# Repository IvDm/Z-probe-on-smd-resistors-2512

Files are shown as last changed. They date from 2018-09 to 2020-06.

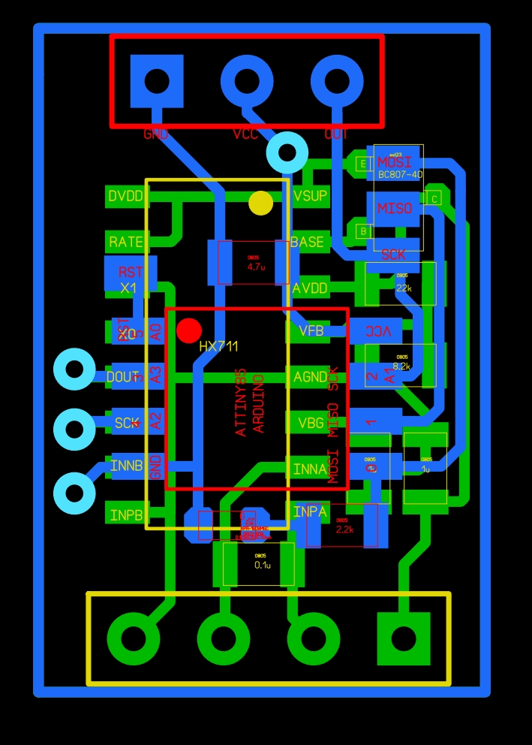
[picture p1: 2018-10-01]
Controller_PCB_TOP.JPG

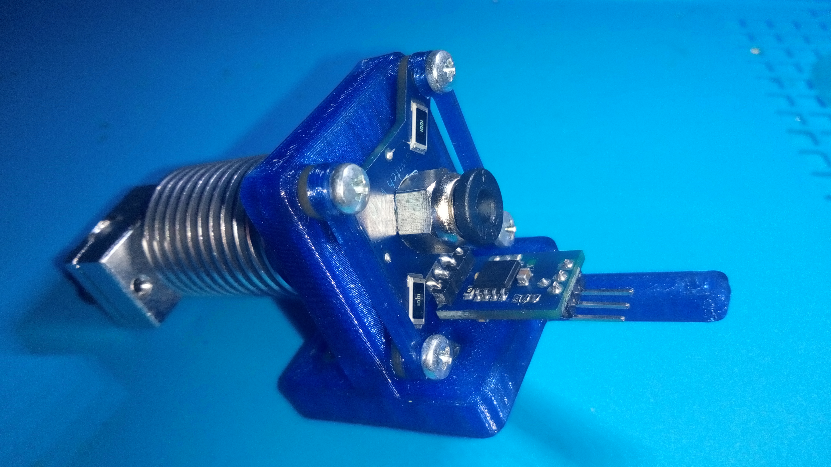
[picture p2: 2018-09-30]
20180930_181452-0.jpg

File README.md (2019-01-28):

# Z-probe-on-smd-resistors-2512
 This project is based on a change in the resistance of resistors under the influence of external factors in particular deformation. The object of the project is to check whether it is possible to use ordinary smd resistors instead of strain gages, and apply this effect to the calibration of the bed 3d printer.
 To implement the project I needed: 4 smd resistor with a resistance of 1 kOhm size 2512, ADC HX711, microcontroller ATtiny 85,pnp transistor bc 807-40 sot23,resistors of size 0805 with a rating of 8.2 kΩ 1 pcs., 22 kΩ 1 pcs., 2.2 kΩ 1 pcs.,capacitors 0805 with a capacity of 4.7u 1pcs, 1u 2pcs, 100n 1pcs, LED 0603 any color 1pcs.,double sided copper clad plate PCB, 3d printer for making plastic parts.Library for the HX711 from here: https://github.com/bogde/HX711
 
 As a result, on a double-sided printed circuit board such a sensor was made:
 


To reduce side effects, the resistors are placed on a two-sided printed circuit board diagonally from both sides. So the sensitivity at the midpoint turned out to be maximum with vertical exposure.To reduce the length of conductors coming from the sensor, it was decided to make a small circuit board for signal processing and place it directly on the sensor board. On the one side of the board is the ADC of the HX711, and on the other the microcontroller ATtiny85.





From the microcontroller, the touch signal is fed to the 3-d printer board.

The boards are interconnected in this way:



To install the sensor on a 3d printer, the following parts were printed:

p80929-190301
p80929-190402
p80930-141411

They are assembled in this way:

strain gage

assembled:



I have a 3d printer "HyperCube" https://www.thingiverse.com/thing:1752766 and installed a sensor on this printer. 
It looks like this:



This is how it looks in action:

https://www.youtube.com/watch?v=x-7hq27BdUY&t=6s

Thus, testing was carried out on the suitability of using SMD resistors for use in the sensor):

https://www.youtube.com/watch?v=UKC9-srKAL4

Oh, and sorry for my English)

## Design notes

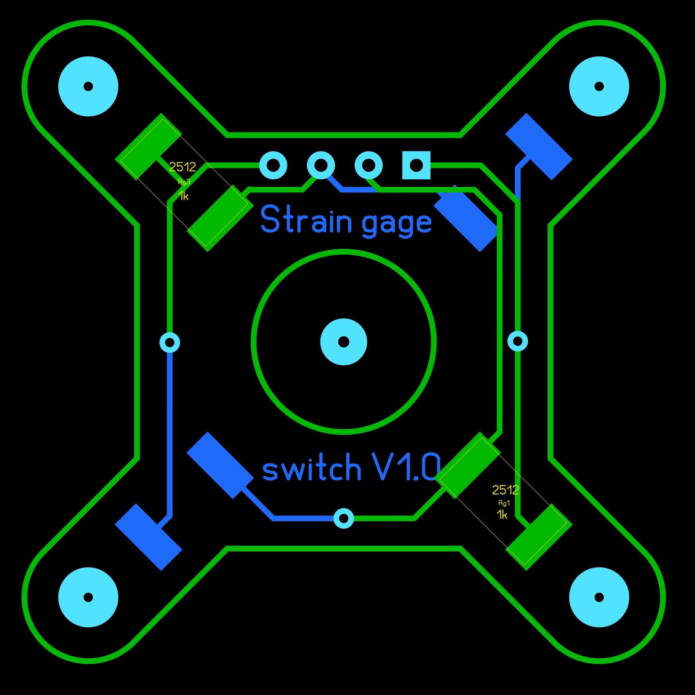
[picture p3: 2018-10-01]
Sensor_PCB_BOTTOM1.JPG

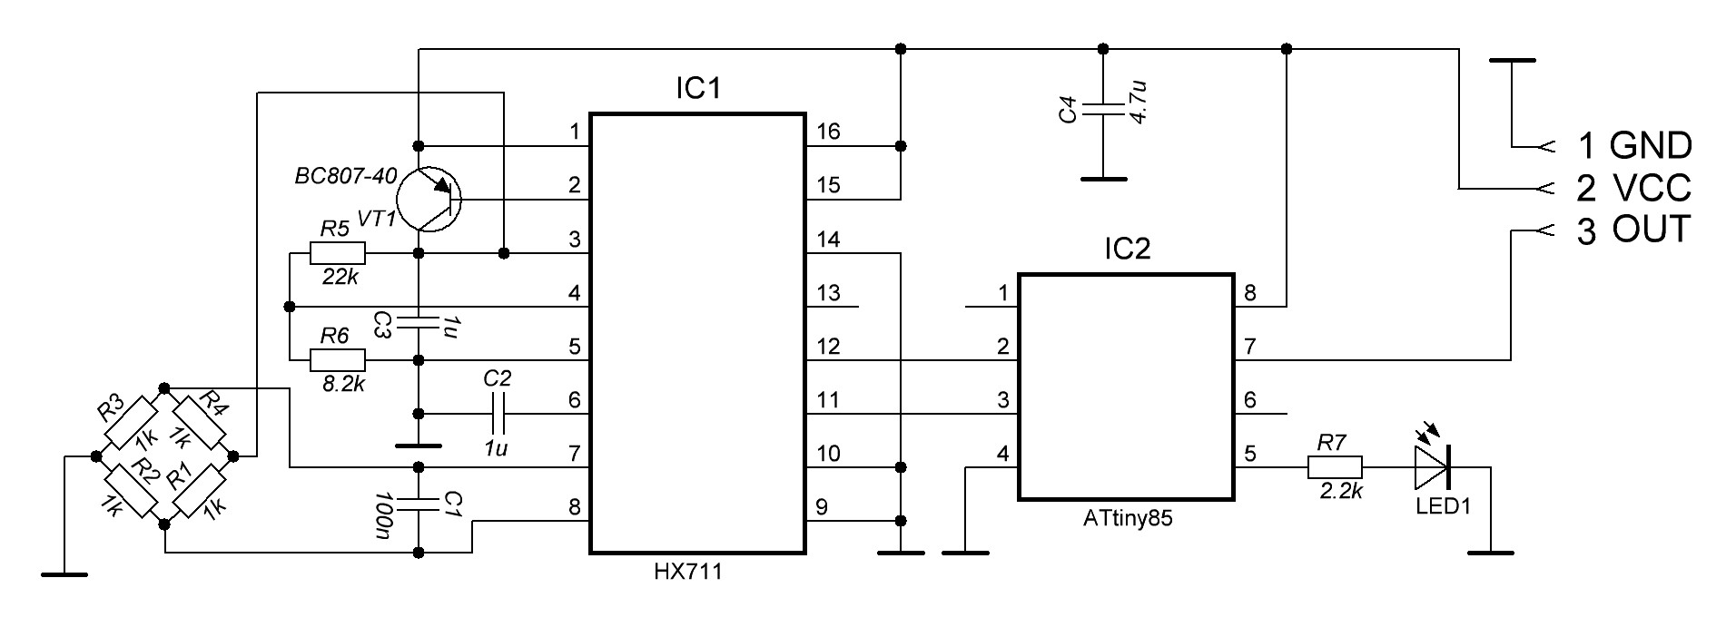
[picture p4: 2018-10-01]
Strain gage electric circuit.JPG

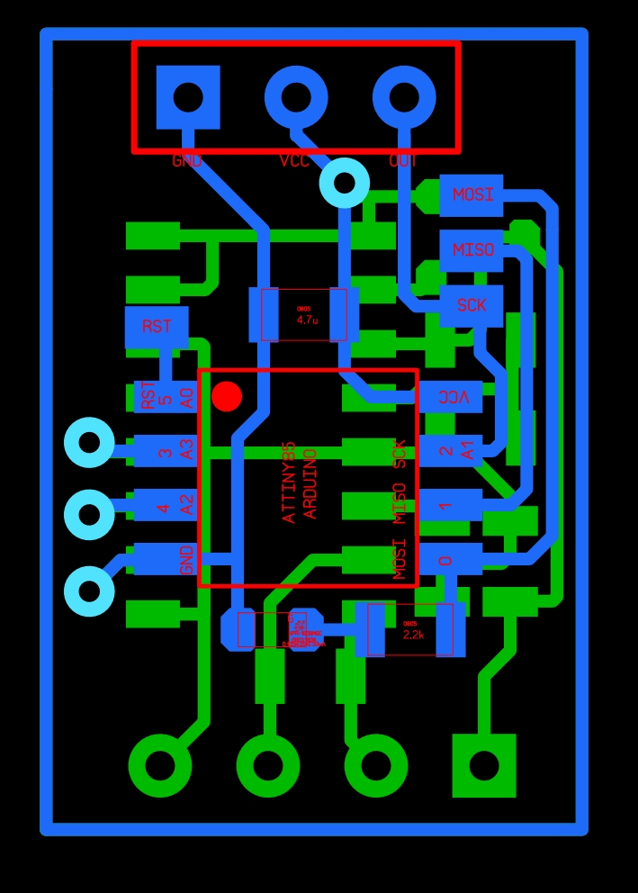
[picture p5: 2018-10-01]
Controller_PCB_TOP1.JPG

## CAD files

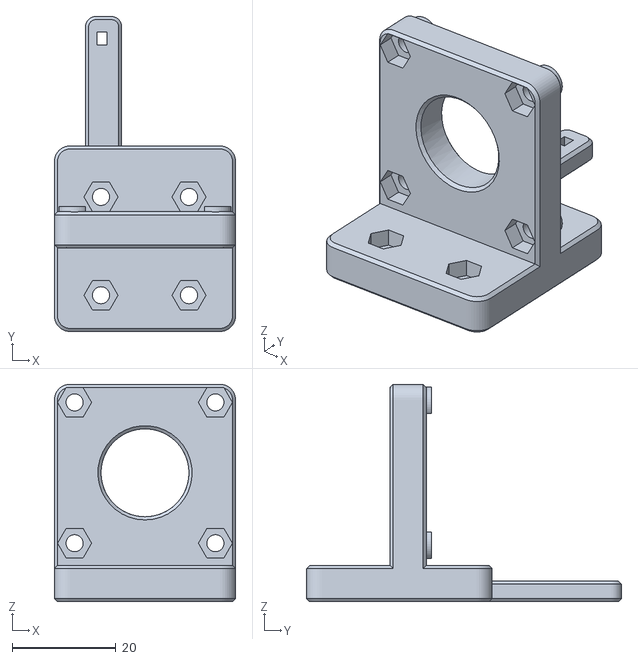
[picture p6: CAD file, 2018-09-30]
extruder bracket.STL
35.0 x 60.9 x 42.0

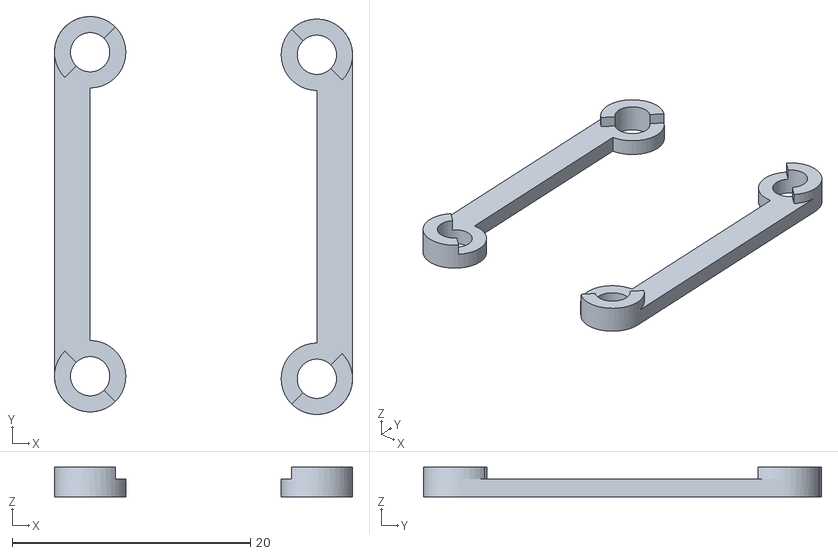
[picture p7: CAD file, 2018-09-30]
double washer .STL
25.0 x 33.4 x 2.50

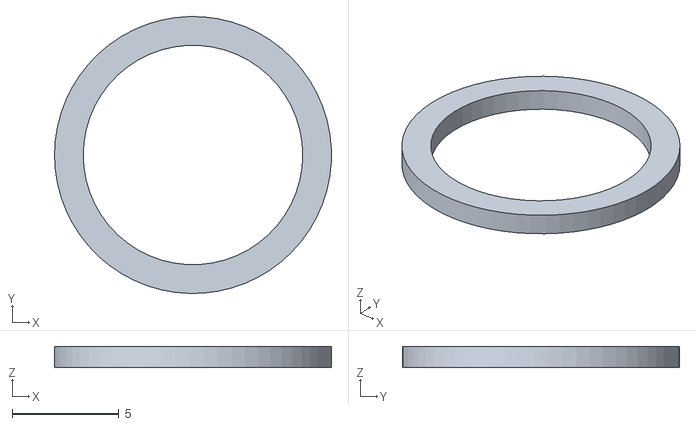
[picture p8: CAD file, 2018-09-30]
Washer 10.3x13x1.STL
13.0 x 13.0 x 1.00

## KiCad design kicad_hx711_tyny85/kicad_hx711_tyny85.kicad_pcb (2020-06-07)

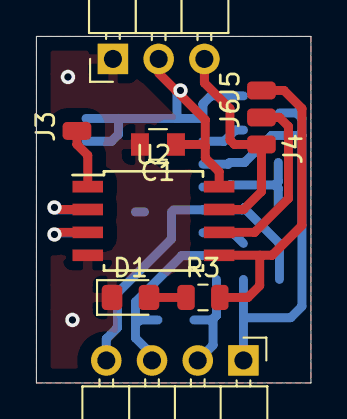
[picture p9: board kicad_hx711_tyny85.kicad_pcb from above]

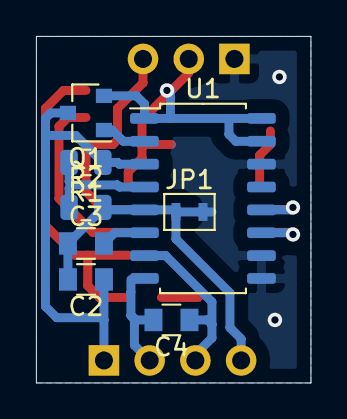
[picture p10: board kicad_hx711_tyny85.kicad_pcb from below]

Board: 2 copper layers, 15.2 x 19.2 mm, 18 parts (8 on the bottom side), 16 nets.

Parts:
C1: 4.7u; C_0805
C2, C3: 1u; C_0805
C4: 0.1u; C_0805
D1: LED; LED_0805_2012Metric_Pad1.15x1.40mm_HandSolder
J1: Conn_01x03_Male; Pin_Header_Angled_1x03_Pitch2.54mm
J2: Conn_01x04_Female; Pin_Header_Angled_1x04_Pitch2.54mm
J3, J4, J5, J6: Conn_01x01_Female; SMD_wire_conn
JP1: Jumper; AnalogGND_jumper
Q1: Q_PNP_BEC; SOT-23
R1: 22k; R_0805_2012Metric
R2: 8k2; R_0805_2012Metric
R3: 2k2; R_0805_2012Metric
U1: HX711; SOP-16_4.55x10.3mm_P1.27mm
U2: ATtiny85V-10SU; SOIJ-8_5.3x5.3mm_P1.27mm

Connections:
DOUT: U1.12, U2.2
GND: C1.2, D1.1, J1.1, JP1.2, U1.9, U1.10, U1.14, U2.4
GNDA: C2.2, C3.1, J2.4, JP1.1, R2.2, U1.5
INNA: C4.1, J2.3, U1.7
INPA: C4.2, J2.2, U1.8
MISO: J6.1, U2.6
MOSI: J5.1, R3.2, U2.5
unnamed: C3.2, U1.6
unnamed: D1.2, R3.1
unnamed: Q1.1, U1.2
unnamed: R1.2, R2.1, U1.4
RST: J3.1, U2.1
SCK: U1.11, U2.3
SCK_OUT: J1.3, J4.1, U2.7
VCC: C1.1, J1.2, Q1.2, U1.1, U1.15, U1.16, U2.8
VDDA: C2.1, J2.1, Q1.3, R1.1, U1.3

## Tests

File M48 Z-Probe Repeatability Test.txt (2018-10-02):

SENDING:M48 P20 X100 Y100 V2
M48 Z-Probe Repeatability Test
echo:busy: processing
echo:busy: processing
1 of 20: z: 0.095
echo:busy: processing
2 of 20: z: 0.102
echo:busy: processing
3 of 20: z: 0.105
echo:busy: processing
4 of 20: z: 0.110
5 of 20: z: 0.112
echo:busy: processing
6 of 20: z: 0.093
echo:busy: processing
7 of 20: z: 0.100
echo:busy: processing
8 of 20: z: 0.080
echo:busy: processing
9 of 20: z: 0.105
echo:busy: processing
10 of 20: z: 0.110
echo:busy: processing
11 of 20: z: 0.090
echo:busy: processing
12 of 20: z: 0.118
echo:busy: processing
13 of 20: z: 0.100
echo:busy: processing
14 of 20: z: 0.102
echo:busy: processing
15 of 20: z: 0.105
16 of 20: z: 0.110
echo:busy: processing
17 of 20: z: 0.093
echo:busy: processing
18 of 20: z: 0.095
echo:busy: processing
19 of 20: z: 0.100
echo:busy: processing
20 of 20: z: 0.102
Finished!
Mean: 0.101375 Min: 0.080 Max: 0.118 Range: 0.038
Standard Deviation: 0.008605

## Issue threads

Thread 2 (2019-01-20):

cool!

jschoch, 2019-01-20:
This is great!  Very cool.  I'm playing with using velostat for a 3d probe and just found this.  I have a

A few questions:

1. how sensitive is this?
2. strain gauges are cheap, did you do this to prove you could?
3. did you test the setup with a strain gauge?
4. did you try this with different resistor values?
5.  Did you try this with plain old pcb traces to act as the strain gauges?

IvDm, 2019-01-22:
Hi! Thank you for your interest in my project. I apologize for the delay in the answer: I just recently saw your message. I will try to answer your questions:

1.In this form, the sensitivity of the sensor is about 90 grams. During testing, it turned out that this is the optimal value for my 3D printer. Sensitivity can be changed by changing the values   in the sketch.

2.Yes, I just wanted to check if it works.)

3.Yes, I used strain gauges and everything worked perfectly.

4.With less resistance, the sensitivity becomes somewhat less. With greater resistance, the sensitivity becomes slightly larger, but the likelihood of false alarms from temperature fluctuations increases.

5.I checked, but I could not make very thin tracks. The minimum thickness of the track at the same time turned out to be 0.1mm. At the same time there is a high probability of obtaining poor-quality trails. With such tracks it works very badly. If you make the track longer, then everything should work well, but this will increase the size of the device.

Harvie, 2019-01-28:
> Did you try this with plain old pcb traces to act as the strain gauges?

I'd really like to get this working!

> false alarms from temperature fluctuations

Well placing such device directly in neighborhood of 3D printer hot end does not sound very good :-)

IvDm, 2019-01-28:
A little off topic, but thanks for your recommendation of my project on the resource Hackday. I did not expect it to be published).

thebrakshow, 2019-03-27:
Hey out of curiosity, why such a large resistor package, is this so that they flex more?

IvDm, 2019-03-27:
Hi. On the contrary: the area of   the active conductive coating is larger, therefore, they can be bent less than, say, resistors of size 2010.

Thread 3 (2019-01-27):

Anybody has spare PCBs?

sanchosk, 2019-01-27:
Not an issue :)
I was just wondering if someone ordered such layout from something like JLCPCB and wants to share the remaining with the world ;)
This looks just perfect, I was thinking about something similar, but this design far exceeds any of my ideas.

Another-Sandman, 2021-12-02:
I could send you one :)

Another-Sandman, 2021-12-02:
Are you still looking to get one pcb ?

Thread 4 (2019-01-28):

Attiny programming

Paulbsh, 2019-01-28:
This is not really an issue but I didnt find a place for my question :)
First off: Great and simple idea with a nice documentation and open source in mind!

I was wondering if you program the Attiny beforehand with a programming rig or after you soldered the attiny to the pcb?

IvDm, 2019-01-28:
Hello. Thank you for your interest in my project. I programmed ATtiny on soldered PCB. This made it possible to adjust the optimum sensitivity of the sensor.

Paulbsh, 2019-01-28:
I see! As far as I remember (it's been a while), the attiny uses 6 pins for programming. Which pins on the soldered pcb did you use for the programming? Could not find something about the programming routine in your (very good) documentation.

IvDm, 2019-01-28:
I apologize if I misled you, I think that some changes should be made to the concept drawing for more clarity.

Paulbsh, 2019-01-28:
Really appreciate your answer!
Thanks!

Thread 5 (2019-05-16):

Make schematics and/or PCB files compatible with KiCad or EAGLE

VinnyCordeiro, 2019-05-16:
The idea of this sensor is ingenious. However, it looks like the PCBs were made using Spring-Layout 6, which is a paid EDA software. If possible, I'd ask for a conversion to KiCad, which is Free/Open Source and widely used by hobbyists.

EAGLE is also another very popular EDA software that have a free version for hobbyists that limits the size and number of layers available. This sensor is small and simple enough to fit these constraints.

Thank you for your time!

Another-Sandman, 2021-12-02:
PLEASE!

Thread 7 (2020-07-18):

FR: better event detection via dual moving average cross-over

Andrei-Pozolotin, 2020-07-18:
1. currently "tare"  happens once, on setup:
https://github.com/IvDm/Z-probe-on-smd-resistors-2512/blob/master/strain_gage_switch_ATtiny85.ino

2. this does not reflect environment changes during long operation:
* parameters temperature drift,
* parameters mechanical creep,
etc.

3. a better way is to use dual moving average cross-over approach,
and eliminate dependency on environment changes i.e.:
```c++
// detect touch events
void process_trigger() {
    const int32_t fast = moving_fast.average();
    const int32_t slow = moving_slow.average();
    const int32_t delta = fast - slow;
    if (delta > 0) {  // react only on proper direction
        if (has_trigger) {
            if (delta < DELTA_PASSIVE) {  // detect turn off
                has_trigger = false;  // remember state
                moving_slow.setup(trigger_slow);  // recover to event start
                process_output (LOW);  // issue turn off
                time_passive = millis();  // report event finish
            }
        } else {
            if (delta > DELTA_ACTIVE) {  // detect turn on
                has_trigger = true;  // remember state
                trigger_slow = slow;  // remember till event finish
                process_output (HIGH);  // issue turn on
                time_active = millis();  // report event start
            }
        }
    }
}
```
4. here is full sketch for arduino/nano:
https://gist.github.com/Andrei-Pozolotin/e7bf413e2438863a04c2497258662bec

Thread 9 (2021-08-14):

Resistor choice

EllaBarker, 2021-08-14:
Since there is no BOM which exact resistor was used?
Also was face-down considered/tested as this has an influence (just like thick and thin film) on the resistance change.
How is the long-term stability of this system? Is there any more drift after the initial phase?

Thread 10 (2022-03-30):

more tiny version of this probe

sl1pkn07, 2022-03-30:
Hi

i want to use this probe with this project https://github.com/madl3x/x-scara

i think i need a little more small version of this probe

what is the minimal size of pcb for make a valid unit? the meassurements of the resistors is the same? what is the thikness i need select for make one?

greetings

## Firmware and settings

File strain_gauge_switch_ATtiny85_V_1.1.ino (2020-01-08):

// CPU ATtiny 85 , clock internal 16MHz
// HX711.DOUT - вывод # A3
// HX711.PD_SCK - вывод # A2
#include "HX711.h"
#define ledPin 0   //Pin indicator LED
#define switchPin 2 //Switch pin
const int LOADCELL_DOUT_PIN = 3;
const int LOADCELL_SCK_PIN = 4;
HX711 scale;

void setup() {
 scale.begin(LOADCELL_DOUT_PIN, LOADCELL_SCK_PIN); 
 pinMode(ledPin, OUTPUT);
 scale.set_scale(6000.f);//This parameter is responsible for the sensor sensitivity. The best results for values from 4000.f to 20000.f
 scale.tare(1); 
}

void loop() {
  long value=0;
  value=scale.get_units(1);
  if(value<=-1 || value>=1)
  {
      digitalWrite(ledPin, HIGH);
      pinMode(switchPin, OUTPUT); 
      digitalWrite(switchPin, LOW);//Pull the switch pin to ground
      delay(20);
      scale.tare(1);
  }
  else
  {
    digitalWrite(ledPin, LOW);
    pinMode(switchPin, INPUT);//switch pin - high impedance 
  }
}
    
   

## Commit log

2018-10-02 Create M48 Z-Probe Repeatability Test.txt
2020-06-02 Update fp-info-cache, kicad_hx711_tyny85-cache.lib, and 4 more files...
    [kicad_hx711_tyny85.kicad_pcb, kicad_hx711_tyny85.sch]
2020-06-02 Split GND-AGND
    [kicad_hx711_tyny85.kicad_pcb]
